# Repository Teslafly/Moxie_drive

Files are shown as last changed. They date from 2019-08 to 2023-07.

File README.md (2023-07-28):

# ABANDONED Moxie_drive
A motor drive based off https://github.com/vedderb/bldc-hardware capable of 75v and 100a continuous for silly electric vehicles

MoxiE-Drive - high power  motor controller
=============

design:
12-60v
120-150 continuous phase amps
based off the vesc 6. has phase shunts

Forged from the remminants of the oppressed vesc 6.
Raised on a diet of endless sphere and equals zero posts.
destined for a fight to the death in hilariously brutal Power Wheels Racing Series.
I give to you, the MoxiE-Drive.

This the Hardware for my derivitive of the Vesc-project.

## Schematic top level


## Layout -made with KiCad!-


## 3D views



Have a look at this post for a tutorial on how to get started:
http://vedder.se/2015/01/vesc-open-source-esc/

Made with KiCad 5

wonderfulfailure.wordpress.com

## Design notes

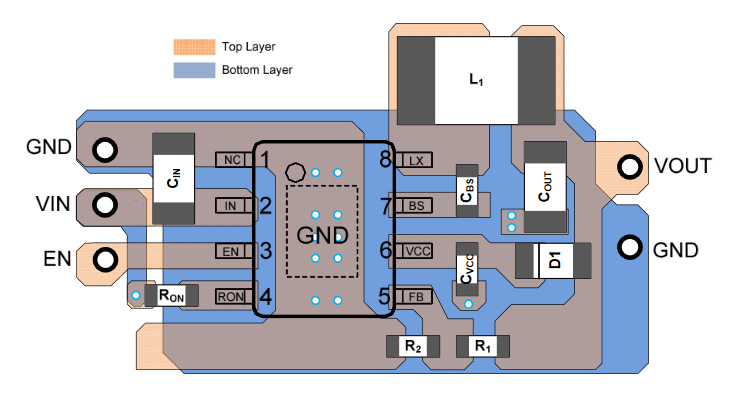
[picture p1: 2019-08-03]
Moxie_Power_stage/sy8502_hv_buck_layout.PNG

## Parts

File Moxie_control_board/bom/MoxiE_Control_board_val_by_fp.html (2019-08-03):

Ref | Qnty | Value | Part | Footprint | Description | Vendor
C101, C110, C304 | 3 | 100n | MoxiE_Control_board-rescue:C-Device | Capacitors_SMD:C_0402
C102, C106, C107, C108, C109, C111, C503, C506, C507 | 9 | 100nf | MoxiE_Control_board-rescue:C-Device | Capacitors_SMD:C_0402
C103, C104, C105, C203 | 4 | 4.7nf | MoxiE_Control_board-rescue:C-Device | Capacitors_SMD:C_0402
C201, C301, C302, C303, C305, C307, C309, C310, C311, C312 | 10 | 2.2u | MoxiE_Control_board-rescue:C-Device | Capacitors_SMD:C_0402
C306, C308 | 2 | 15p | MoxiE_Control_board-rescue:C-Device | Capacitors_SMD:C_0402
C501, C508 | 2 | 2.2uf | MoxiE_Control_board-rescue:C-Device | Capacitors_SMD:C_0603
C509 | 1 | 100uf | MoxiE_Control_board-rescue:CP-Device | Capacitors_Tantalum_SMD:CP_Tantalum_Case-B_EIA-3528-21_Reflow
C510 | 1 | NP | MoxiE_Control_board-rescue:C-Device | Capacitors_SMD:C_0402
D301 | 1 | TPD2EUSB30DRTR | MoxiE_drive-rescue:TPD2EUSB30DRTR-dk_TVS-Diodes | digikey-footprints:SOT-3
D302 | 1 | BLUE | MoxiE_Control_board-rescue:LED_ALT-Device | LEDs:LED_0603
D303 | 1 | GREEN | MoxiE_Control_board-rescue:LED_ALT-Device | LEDs:LED_0603
D304 | 1 | RED | MoxiE_Control_board-rescue:LED_ALT-Device | LEDs:LED_0603
F401 | 1 | 0.5A polyfuse | MoxiE_Control_board-rescue:Polyfuse_Small-Device | Resistors_SMD:R_1812
IC201 | 1 | TCAN332D | MoxiE_drive_symbol_lib:TCAN332D | SO8
J101 | 1 | USB_B_Micro | MoxiE_drive-rescue:USB_B_Micro-Connector_Specialized | Connectors_USB:USB_Micro-B_Vertical_Molex-105133-0001
J102 | 1 | Conn_02x14_Odd_Even | MoxiE_Control_board-rescue:Conn_02x14_Odd_Even-Connector_Generic | moxie-drive-custom:FLE-113-01-G-DV
J301 | 1 | SWD | MoxiE_Control_board-rescue:Conn_01x05-Connector_Generic | Connectors_JST:JST_SH_SM06B-SRSS-TB_06x1.00mm_Angled
J401, J402, J403 | 3 | Conn_01x02 | MoxiE_Control_board-rescue:Conn_01x02-Connector_Generic | Connectors_JST:JST_PH_B2B-PH-K_02x2.00mm_Straight
K101 | 1 | SERVO | MoxiE_Control_board-rescue:Conn_01x03-Connector_Generic | Connectors_JST:JST_PH_B3B-PH-K_03x2.00mm_Straight
L501 | 1 | 3.3uH | MoxiE_drive-rescue:INDUCTOR-MyCustomLib | Mas_custom_parts:L_Bourns_SRN-4018
P101 | 1 | CANBUS | MoxiE_Control_board-rescue:Conn_01x04-Connector_Generic | Connectors_JST:JST_PH_B4B-PH-K_04x2.00mm_Straight
P102 | 1 | Serial3 | MoxiE_Control_board-rescue:Conn_01x04-Connector_Generic | Connectors_JST:JST_SH_SM04B-SRSS-TB_04x1.00mm_Angled
P103 | 1 | CTRL_SIGNALS | MoxiE_Control_board-rescue:Conn_01x07-Connector_Generic | Connectors_JST:JST_PH_B7B-PH-K_07x2.00mm_Straight
P104 | 1 | SPI | MoxiE_Control_board-rescue:Conn_01x06-Connector_Generic | Connectors_JST:JST_SH_SM06B-SRSS-TB_06x1.00mm_Angled
P105 | 1 | Serial1/tim4 | MoxiE_Control_board-rescue:Conn_01x04-Connector_Generic | Connectors_JST:JST_SH_SM04B-SRSS-TB_04x1.00mm_Angled
P106 | 1 | I2C | MoxiE_Control_board-rescue:Conn_01x04-Connector_Generic | Connectors_JST:JST_SH_SM04B-SRSS-TB_04x1.00mm_Angled
P107 | 1 | HALL/Encoder | MoxiE_Control_board-rescue:Conn_01x06-Connector_Generic | Connectors_JST:JST_PH_B6B-PH-K_06x2.00mm_Straight
Q401, Q402 | 2 | IRLML6344TRPBF | MoxiE_drive-rescue:IRLML6344TRPBF-dk_Transistors-FETs-MOSFETs-Single | digikey-footprints:SOT-23-3
R101, R111, R112, R113, R114, R115, R116, R117, R118, R119 | 10 | 100R | MoxiE_Control_board-rescue:R-Device | Resistors_SMD:R_0402
R102, R103 | 2 | 100k | MoxiE_Control_board-rescue:R-Device | Resistors_SMD:R_0402
R104, R105 | 2 | 22R | MoxiE_Control_board-rescue:R-Device | Resistors_SMD:R_0402
R106, R107, R108 | 3 | 2k2 | MoxiE_Control_board-rescue:R-Device | Resistors_SMD:R_0402
R109 | 1 | 10k | MoxiE_Control_board-rescue:R-Device | Resistors_SMD:R_0402
R110 | 1 | 0R | MoxiE_Control_board-rescue:R-Device | Resistors_SMD:R_0402
R201, R202 | 2 | 120R | MoxiE_Control_board-rescue:R-Device | Resistors_SMD:R_0603
R301, R302, R303, R501 | 4 | 1k | MoxiE_Control_board-rescue:R-Device | Resistors_SMD:R_0402
R502 | 1 | R33.2k 0.1% | MoxiE_Control_board-rescue:R-Device | Resistors_SMD:R_0402
R503 | 1 | 10k 0.1% | MoxiE_Control_board-rescue:R-Device | Resistors_SMD:R_0402
U301 | 1 | STM32F40X_LQFP64 | MoxiE_drive_symbol_lib:STM32F40X_LQFP64 | crf1:lqfp64_pad_mod
U502 | 1 | TPS561201 | MoxiE_Control_board-rescue:TPS563200-Regulator_Switching | TO_SOT_Packages_SMD:SOT-23-6
X301 | 1 | 8MHz 10ppm | MoxiE_drive_symbol_lib:CRYSTAL_SMD | Oscillators:Oscillator_SMD_EuroQuartz_XO53-4pin_5.0x3.2mm

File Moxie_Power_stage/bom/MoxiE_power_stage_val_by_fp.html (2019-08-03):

Ref | Qnty | Value | Part | Footprint | Description | Vendor
C101, C102, C103, C104, C105 | 5 | 470uf 80v | Device:CP1 | Mas_custom_parts:CP_Radial_D12.5mm_P5.00mm | Polarised capacitor
C201 | 1 | 2.2uF_100V | Device:C | pkl_dipol:C_1206 | Unpolarized capacitor
C202 | 1 | 0.1uf_100V | Device:C | pkl_dipol:C_0603 | Unpolarized capacitor
C203 | 1 | 0.1uf | Device:C | pkl_dipol:R_0402 | Unpolarized capacitor
C204 | 1 | 0.1uf | Device:C | pkl_dipol:C_0402 | Unpolarized capacitor
C205 | 1 | 4.7nf | Device:C | pkl_dipol:C_0402 | Unpolarized capacitor
C206, C301, C310, C401, C410, C501, C510 | 7 | 1uf | Device:C | pkl_dipol:C_0603 | Unpolarized capacitor
C207 | 1 | 100uf 25v | Device:CP1 | Capacitors_THT:CP_Radial_D8.0mm_P3.50mm | Polarised capacitor
C302, C303, C304, C305, C306, C307, C308, C309, C311, C402, C403, C404, C405, C406, C407, C408, C409, C411, C502, C503, C504, C505, C506, C507, C508, C509, C511 | 27 | 100v_1.0uF | Device:C | pkl_dipol:C_1206 | Unpolarized capacitor
C315, C415, C515 | 3 | 2.2u | Device:C | pkl_dipol:C_0402 | Unpolarized capacitor
D201 | 1 | 100v 200ma | Device:D | Diodes_SMD:D_SOD-323 | Diode
J101 | 1 | Conn_02x13_Counter_Clockwise | Connector_Generic:Conn_02x13_Counter_Clockwise | moxie-drive-custom:FLE-113-01-G-DV | Generic connector, double row, 02x13, counter clockwise pin numbering scheme (similar to DIP packge numbering), script generated (kicad-library-utils/schlib/autogen/connector/)
J201, J202 | 2 | Conn_01x02 | Connector_Generic:Conn_01x02 | Connectors_JST:JST_PH_B2B-PH-K_02x2.00mm_Straight | Generic connector, single row, 01x02, script generated (kicad-library-utils/schlib/autogen/connector/)
L201 | 1 | 100uh 2.5A | Device:L_Core_Ferrite | Inductors_SMD:L_12x12mm_h8mm | Inductor with Ferrite Core
MK101, MK102 | 2 | Mounting_Hole | Mechanical:Mounting_Hole | Mounting_Holes:MountingHole_3.2mm_M3 | Mounting Hole without connection
MK103, MK104, MK105, MK106 | 4 | Mounting_Hole | Mechanical:Mounting_Hole | Mounting_Holes:MountingHole_3.2mm_M3_Pad_Via | Mounting Hole without connection
NT301, NT401, NT501 | 3 | Net-Tie_2 | Device:Net-Tie_2 | NetTie:NetTie-2_SMD_Pad0.5mm | Net Tie, 2 pins
P101, P102, P105 | 3 | PHASE_3 | Connector_Generic:Conn_01x01 | Mas_custom_parts:large_wire_pad | Generic connector, single row, 01x01, script generated (kicad-library-utils/schlib/autogen/connector/)
P103 | 1 | PHASE_1 | Connector_Generic:Conn_01x01 | Mas_custom_parts:large_wire_pad | Generic connector, single row, 01x01, script generated (kicad-library-utils/schlib/autogen/connector/)
P104 | 1 | PHASE_2 | Connector_Generic:Conn_01x01 | Mas_custom_parts:large_wire_pad | Generic connector, single row, 01x01, script generated (kicad-library-utils/schlib/autogen/connector/)
Q301, Q302, Q303, Q304, Q305, Q306, Q401, Q402, Q403, Q404, Q405, Q406, Q501, Q502, Q503, Q504, Q505, Q506 | 18 | TPH2R608NH,L1Q | Device:Q_NMOS_DGS | moxie-drive-custom:SOP8_Advance | Transistor N-MOSFET (general)
R101 | 1 | 100k | Device:R | pkl_dipol:R_0402 | Resistor
R102 | 1 | 1k | Device:R | pkl_dipol:R_0402 | Resistor
R201 | 1 | 100k | Device:R | pkl_dipol:R_0603 | Resistor
R202, R601 | 2 | 10k | Device:R | pkl_dipol:R_0402 | Resistor
R203 | 1 | 2MΩ | Device:R | pkl_dipol:R_0603 | Resistor
R204 | 1 | 20k | Device:R | pkl_dipol:R_0402 | Resistor
R205 | 1 | 2.2k | Device:R | pkl_dipol:R_0402 | Resistor
R301, R302, R401, R402, R501, R502 | 6 | 2k2 | Device:R | pkl_dipol:R_0402 | Resistor
R303, R304, R305, R306, R307, R308, R403, R404, R405, R406, R407, R408, R503, R504, R505, R506, R507, R508 | 18 | 10R | Device:R | pkl_dipol:R_0402 | Resistor
R309, R312, R409, R412, R509, R512 | 6 | 1.0mΩ | Device:R | NetTie:NetTie-2_SMD_Pad2.0mm | Resistor
R310, R410, R510 | 3 | 0.5mΩ | Device:R | moxie-drive-custom:R_2512_shunt_vishay | Resistor
R311, R411, R511 | 3 | 1.0mΩ | Device:R | moxie-drive-custom:R_2512_shunt_vishay | Resistor
R313, R413, R513, R603, R605 | 5 | 39k | Device:R | pkl_dipol:R_0603 | Resistor
R314, R414, R514, R604, R606 | 5 | 2k2 | Device:R | pkl_dipol:R_0603 | Resistor
R602 | 1 | 10k ntc | Device:R | pkl_dipol:R_0402 | Resistor
U201 | 1 | SY8502 | MoxiE_power_stage-rescue:SY8502-MAS_Power | Mas_custom_parts:SO8-E
U301, U401, U501 | 3 | MIC4605-1YMT | MoxiE_power_stage-rescue:MIC4065-1YMT-MAS_Power | moxie-drive-custom:TDFN2525-10ld
U302, U402, U502 | 3 | ACS711 | MoxiE_power_stage-rescue:ACS711-MAS_Power | Mas_custom_parts:ACS711KEX

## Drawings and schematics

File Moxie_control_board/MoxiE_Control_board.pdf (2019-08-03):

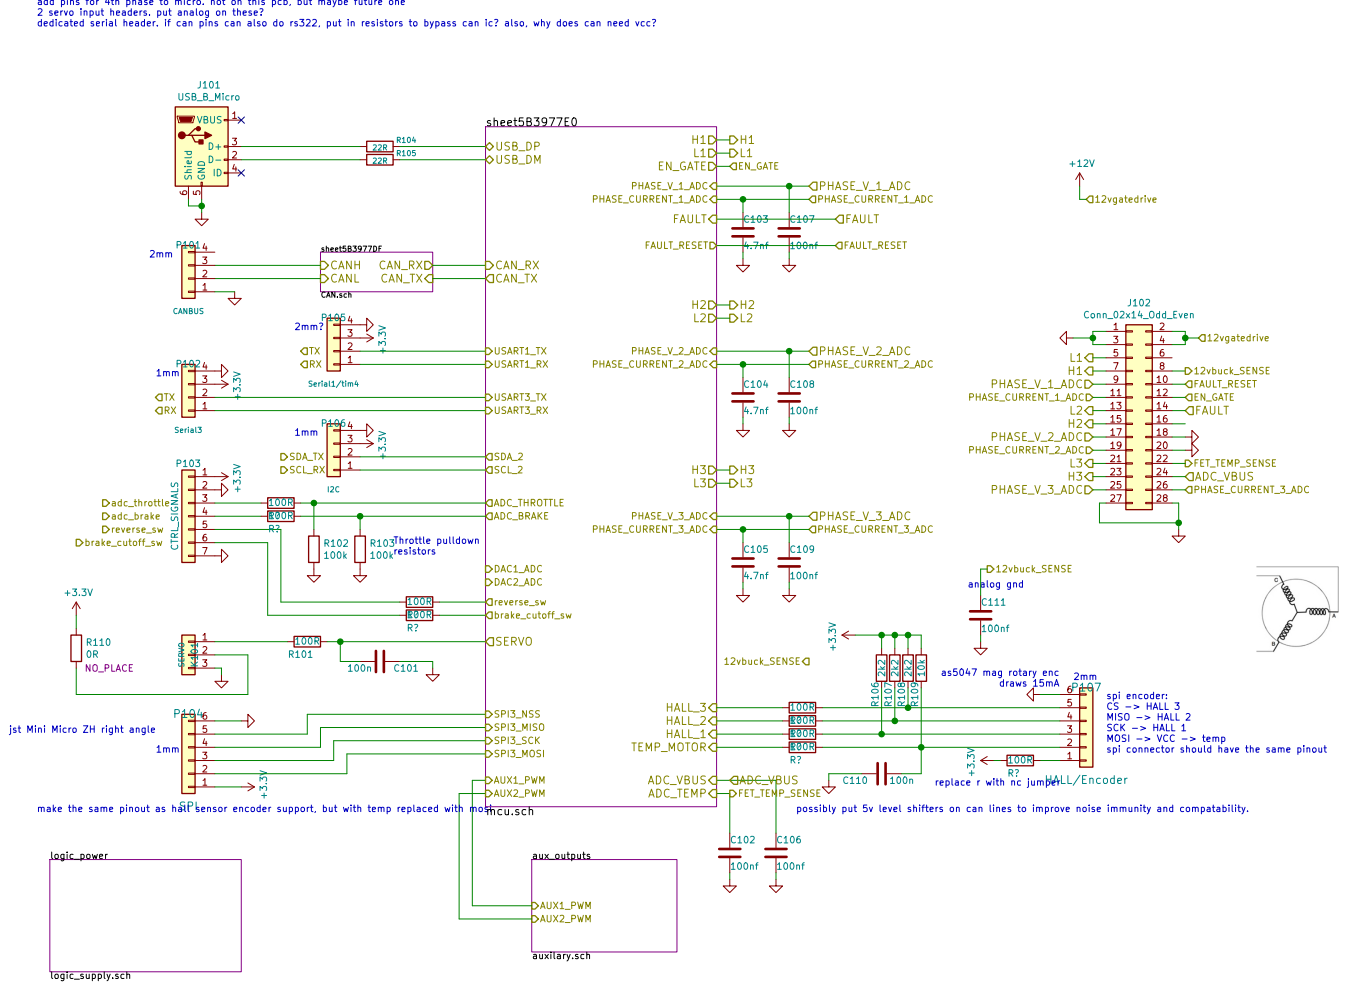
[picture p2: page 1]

add pins for 4th phase to micro. not on this pcb, but maybe future one
2 servo input headers. put analog on these?
dedicated serial header. if can pins can also do rs322, put in resistors to bypass can ic? also, why does can need vcc?

as5047 mag rotary enc draws 15mA

spi encoder: CS -> HALL 3 MISO -> HALL 2 SCK -> HALL 1 MOSI -> VCC -> temp

jst Mini Micro ZH right angle

replace r with nc jumper

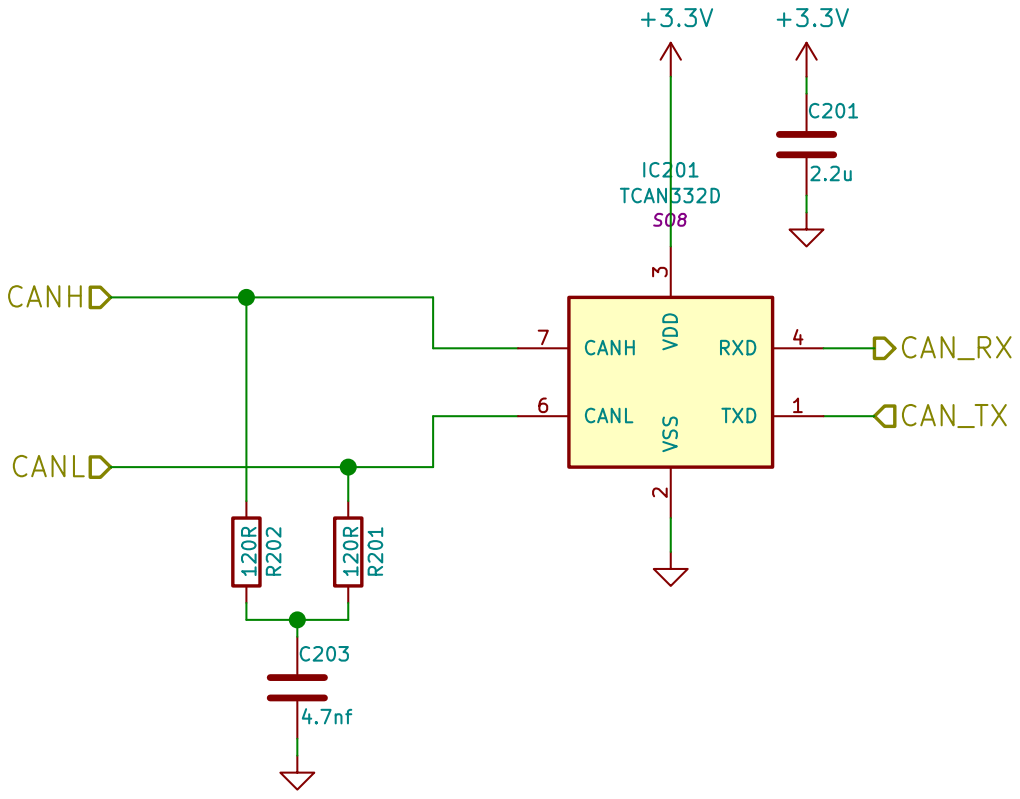
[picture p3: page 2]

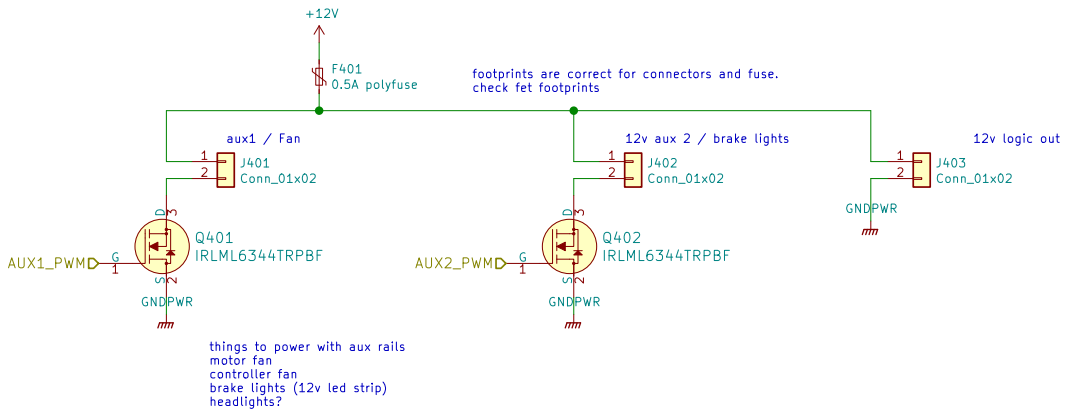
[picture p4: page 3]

footprints are correct for connectors and fuse.
check fet footprints

things to power with aux rails motor fan

controller fan
brake lights (12v led strip)

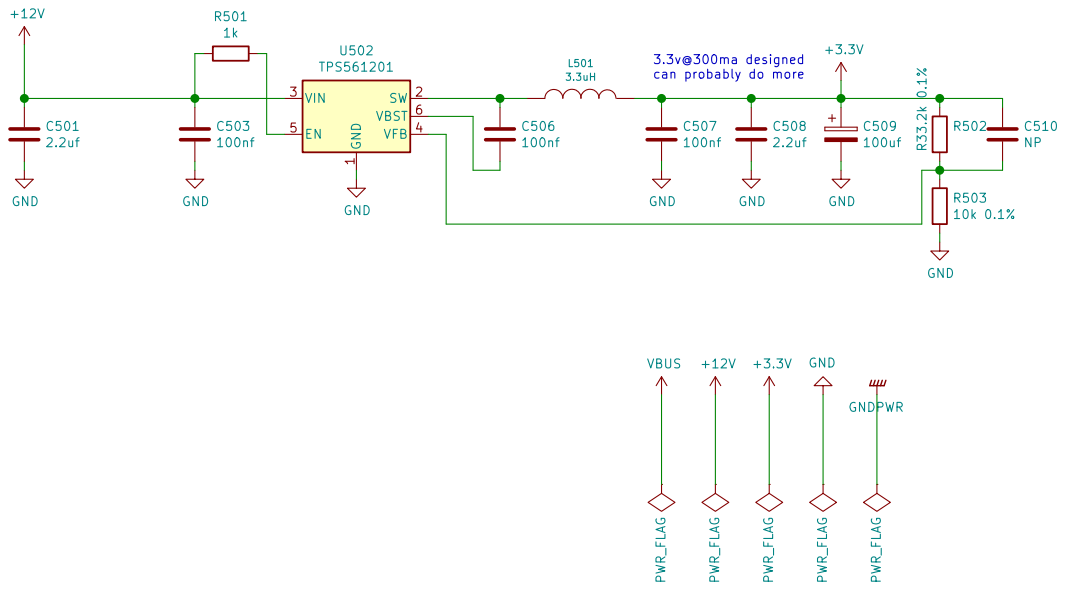
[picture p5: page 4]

can probably do more C501

1 SW 2 VIN 3 VFB 4 EN 5 VBST 6 U502 TPS561201 L501

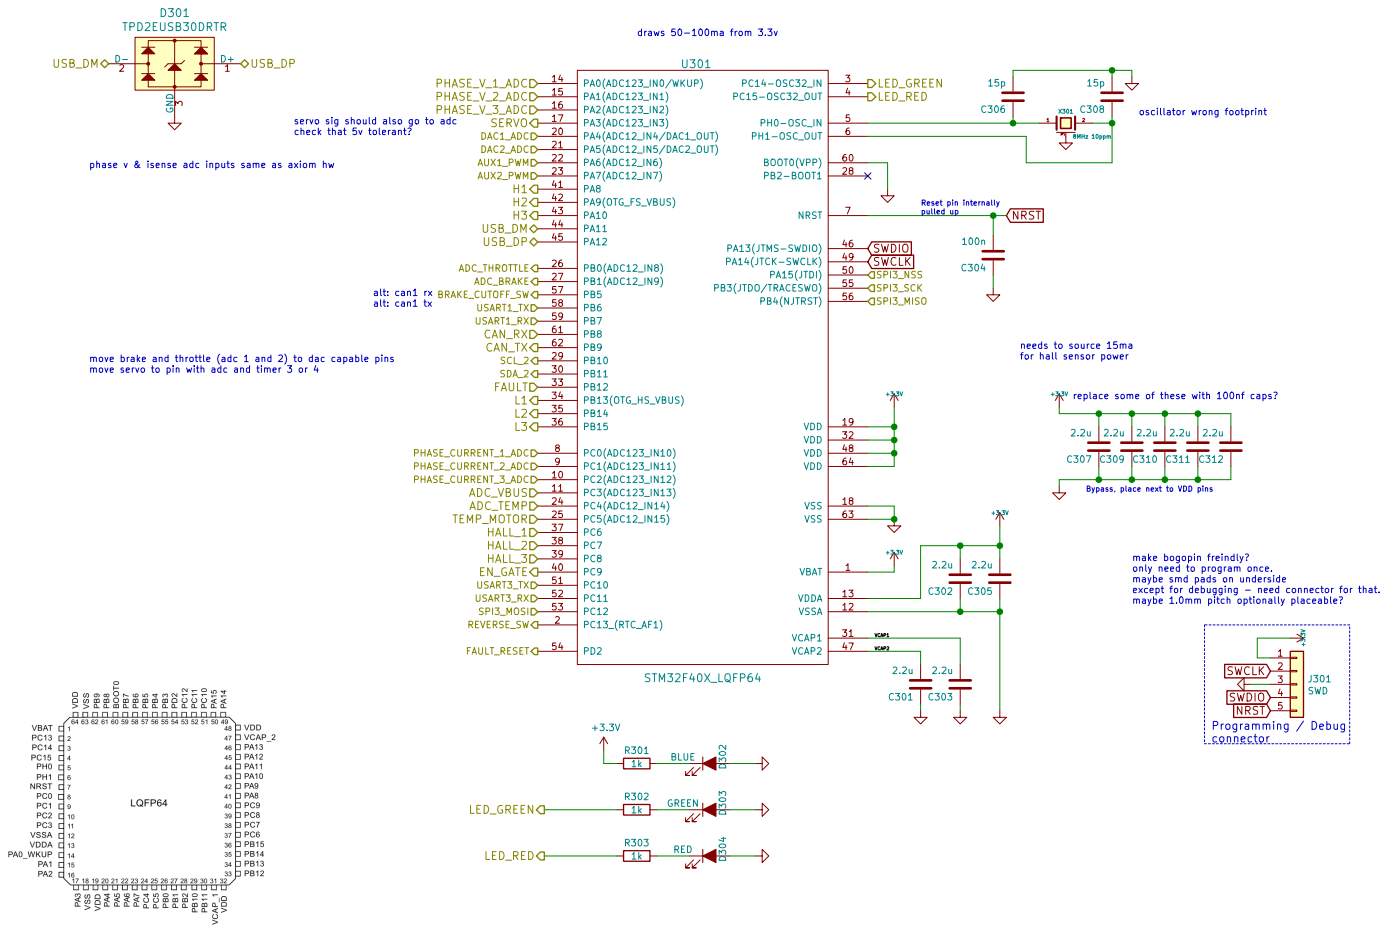
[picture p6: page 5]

replace some of these with 100nf caps? SPI3_NSS

servo sig should also go to adc

phase v & isense adc inputs same as axiom hw

alt: can1 rx alt: can1 tx

Bypass, place next to VDD pins CAN_RX
CAN_TX

move brake and throttle (adc 1 and 2) to dac capable pins
move servo to pin with adc and timer 3 or 4

only need to program once.
maybe smd pads on underside
except for debugging - need connector for that.

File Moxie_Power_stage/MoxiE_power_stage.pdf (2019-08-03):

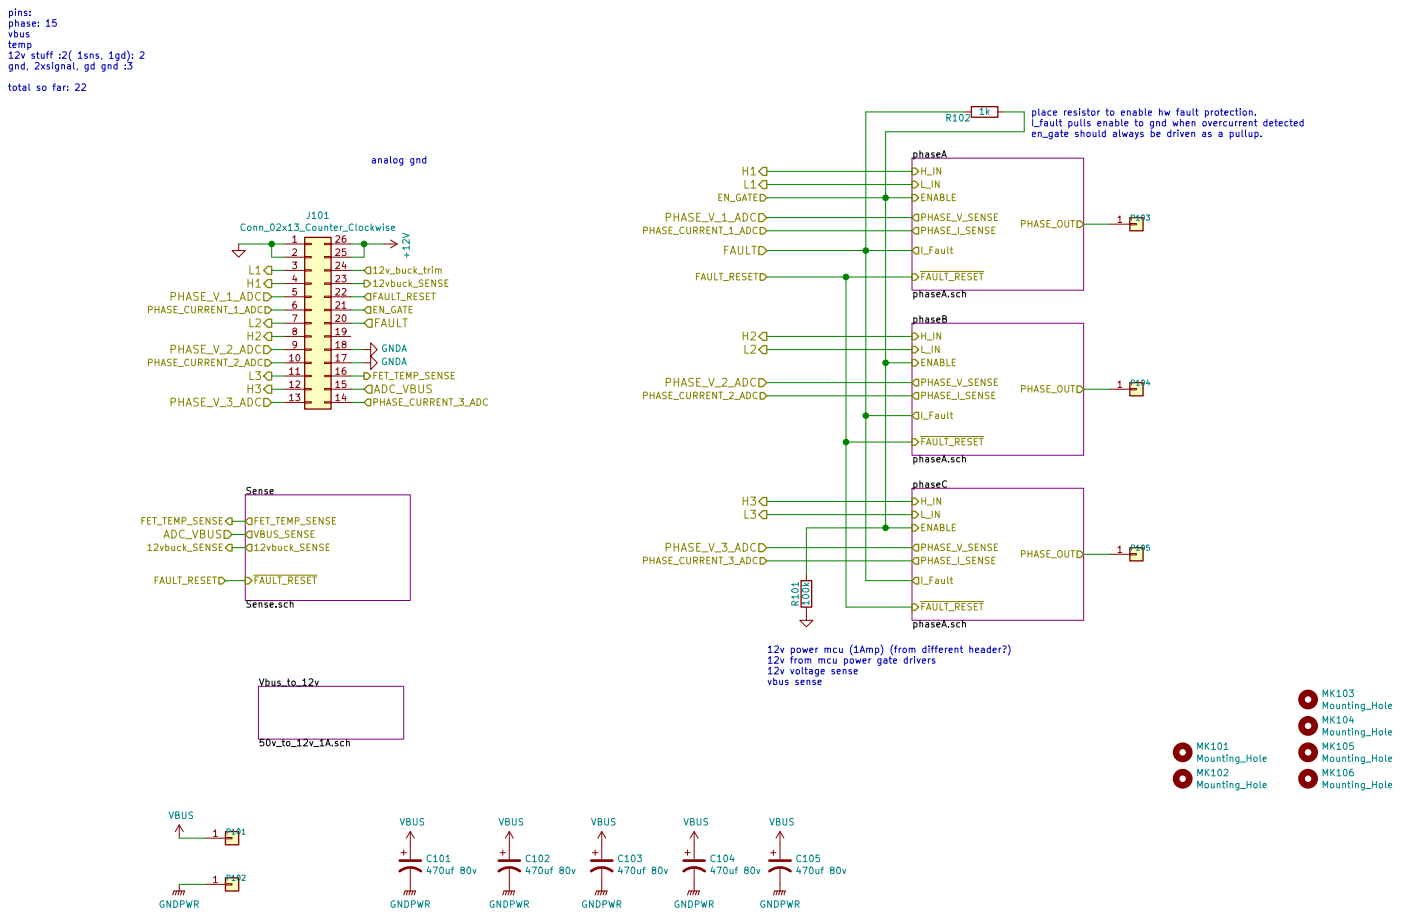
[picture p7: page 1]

I_fault pulls enable to gnd when overcurrent detected
en_gate should always be driven as a pullup.

12v from mcu power gate drivers
12v voltage sense

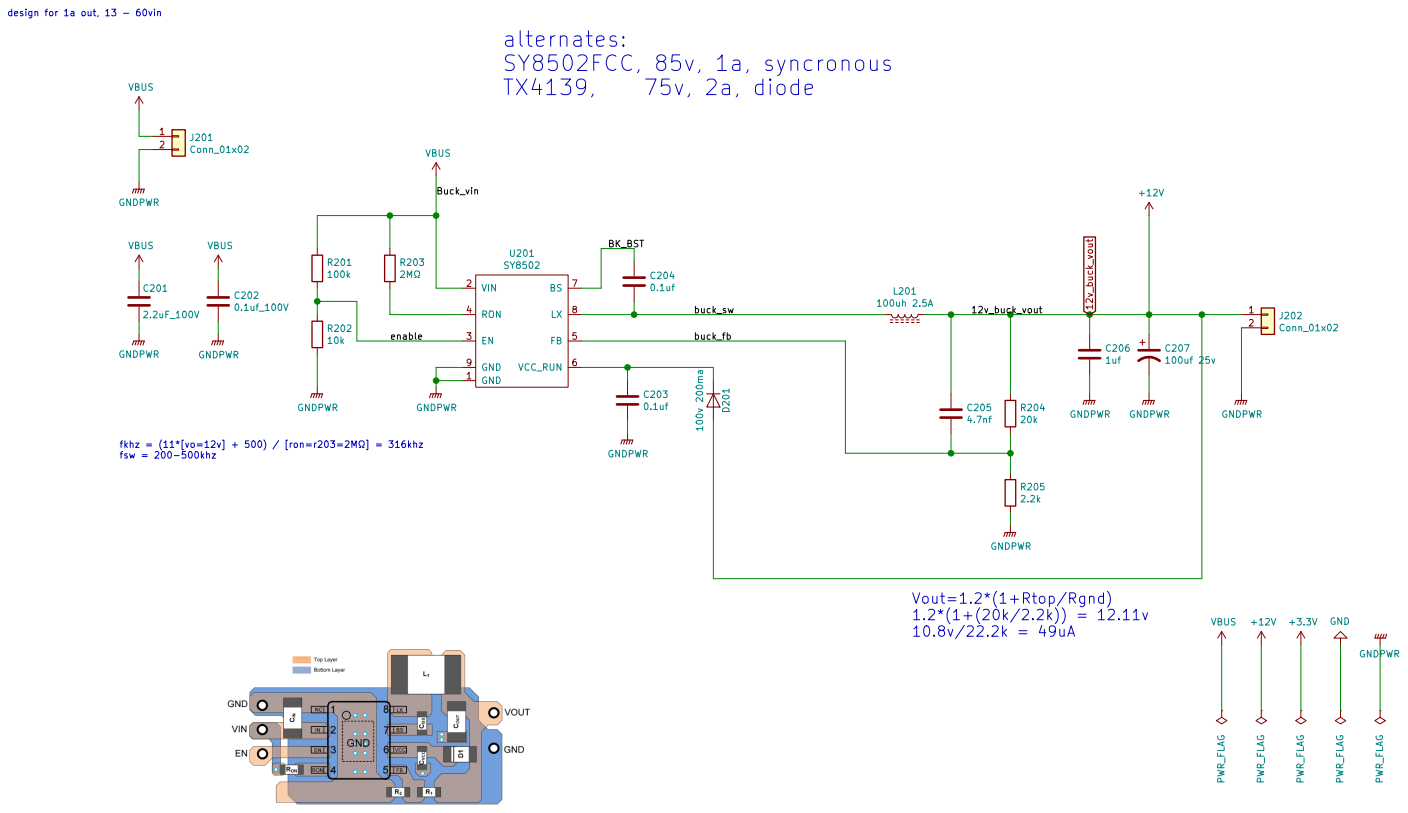
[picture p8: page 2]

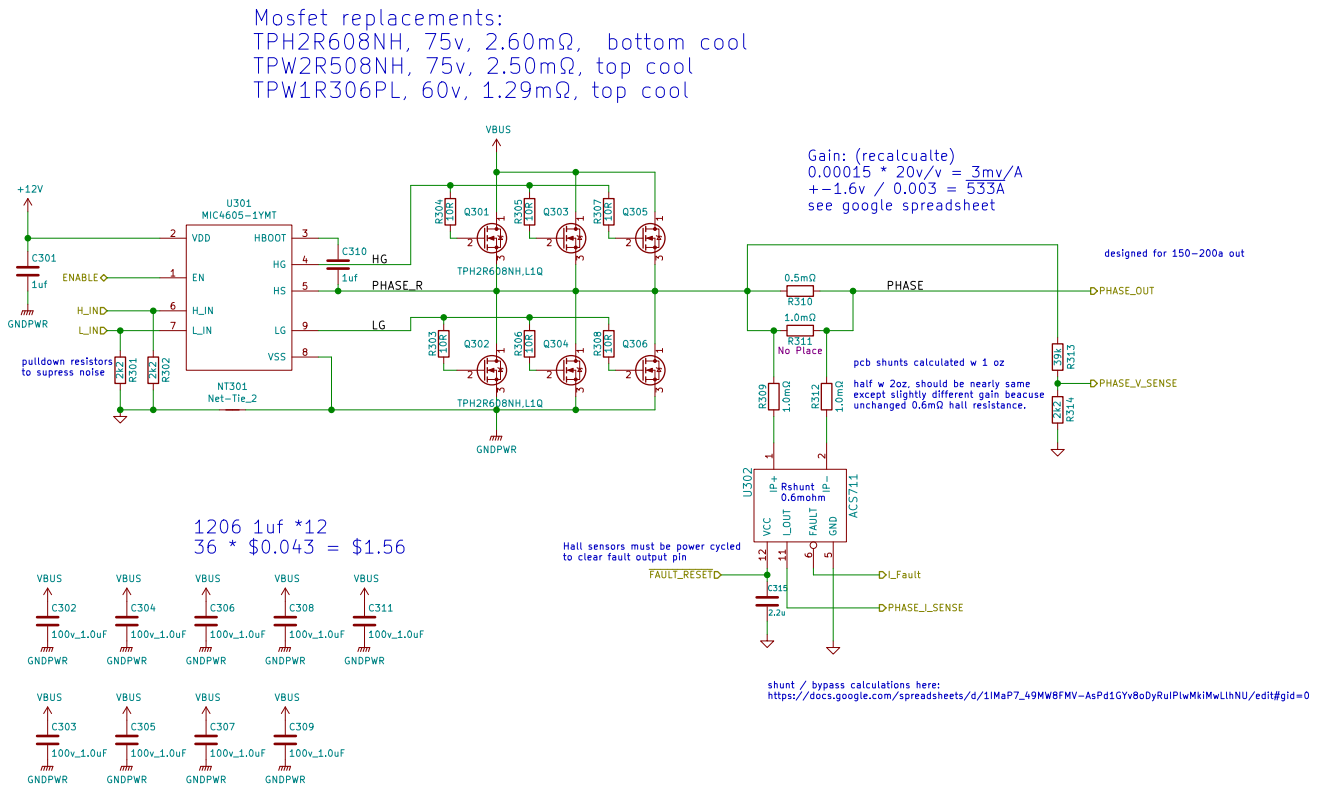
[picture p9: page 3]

pcb shunts calculated w 1 oz

half w 2oz, should be nearly same
except slightly different gain beacuse

FAULT_RESET Hall sensors must be power cycled

shunt / bypass calculations here:
https://docs.google.com/spreadsheets/d/1IMaP7_49MW8FMV-AsPd1GYv8oDyRuIPlwMkiMwLlhNU/edit#gid=0

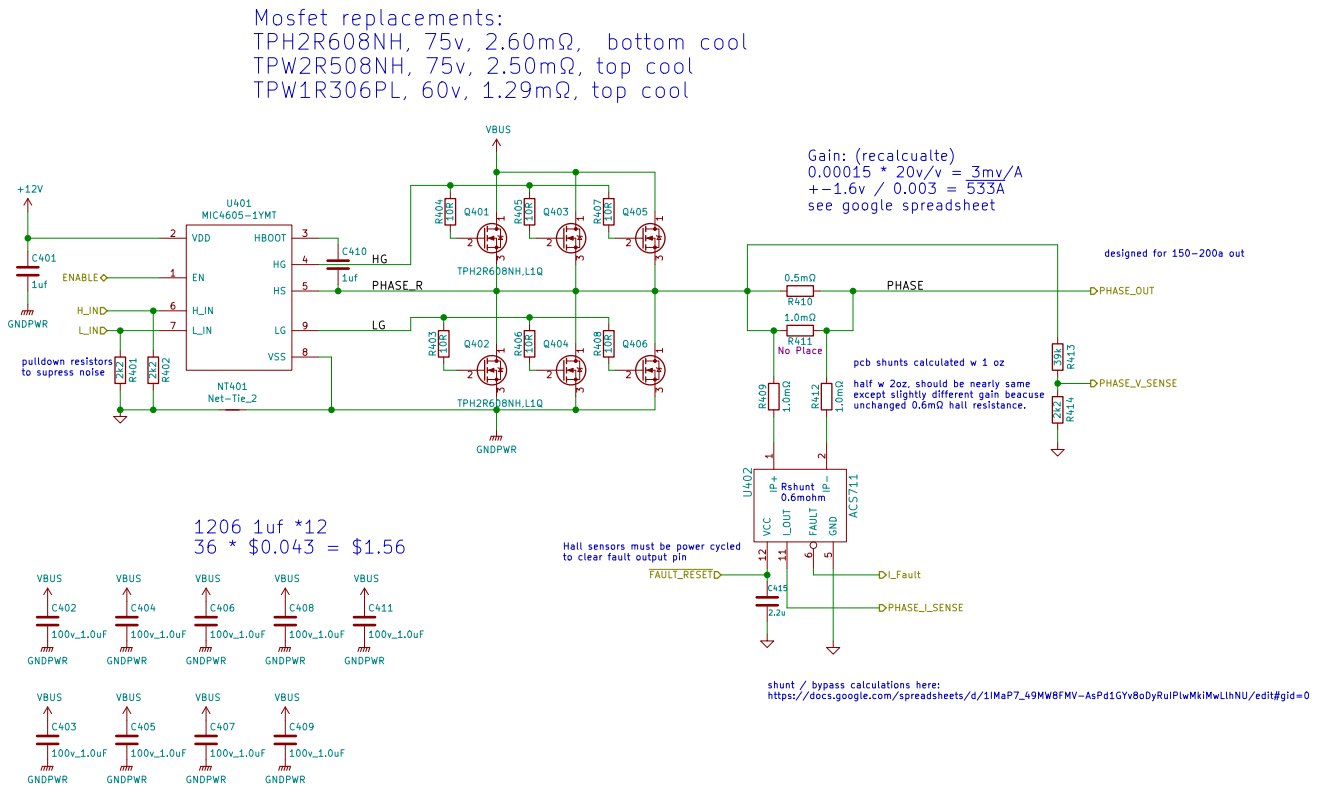
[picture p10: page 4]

pcb shunts calculated w 1 oz

half w 2oz, should be nearly same
except slightly different gain beacuse

FAULT_RESET Hall sensors must be power cycled

shunt / bypass calculations here:
https://docs.google.com/spreadsheets/d/1IMaP7_49MW8FMV-AsPd1GYv8oDyRuIPlwMkiMwLlhNU/edit#gid=0

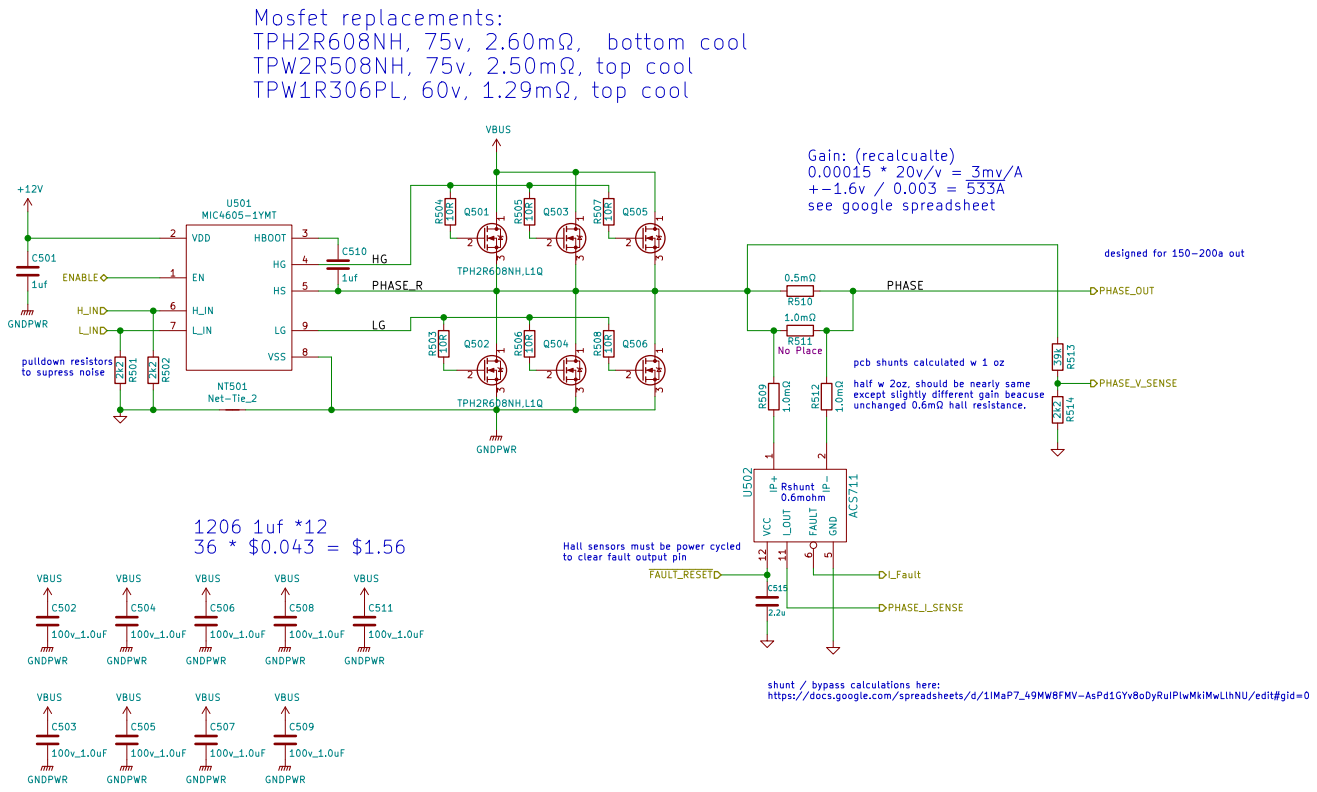
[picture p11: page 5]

pcb shunts calculated w 1 oz

half w 2oz, should be nearly same
except slightly different gain beacuse

FAULT_RESET Hall sensors must be power cycled

shunt / bypass calculations here:
https://docs.google.com/spreadsheets/d/1IMaP7_49MW8FMV-AsPd1GYv8oDyRuIPlwMkiMwLlhNU/edit#gid=0

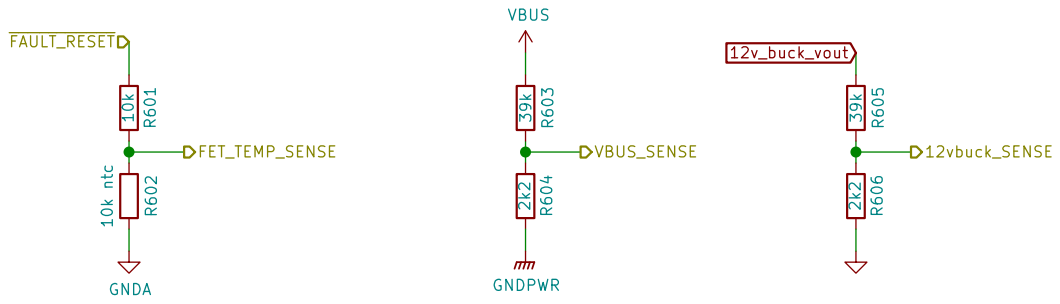
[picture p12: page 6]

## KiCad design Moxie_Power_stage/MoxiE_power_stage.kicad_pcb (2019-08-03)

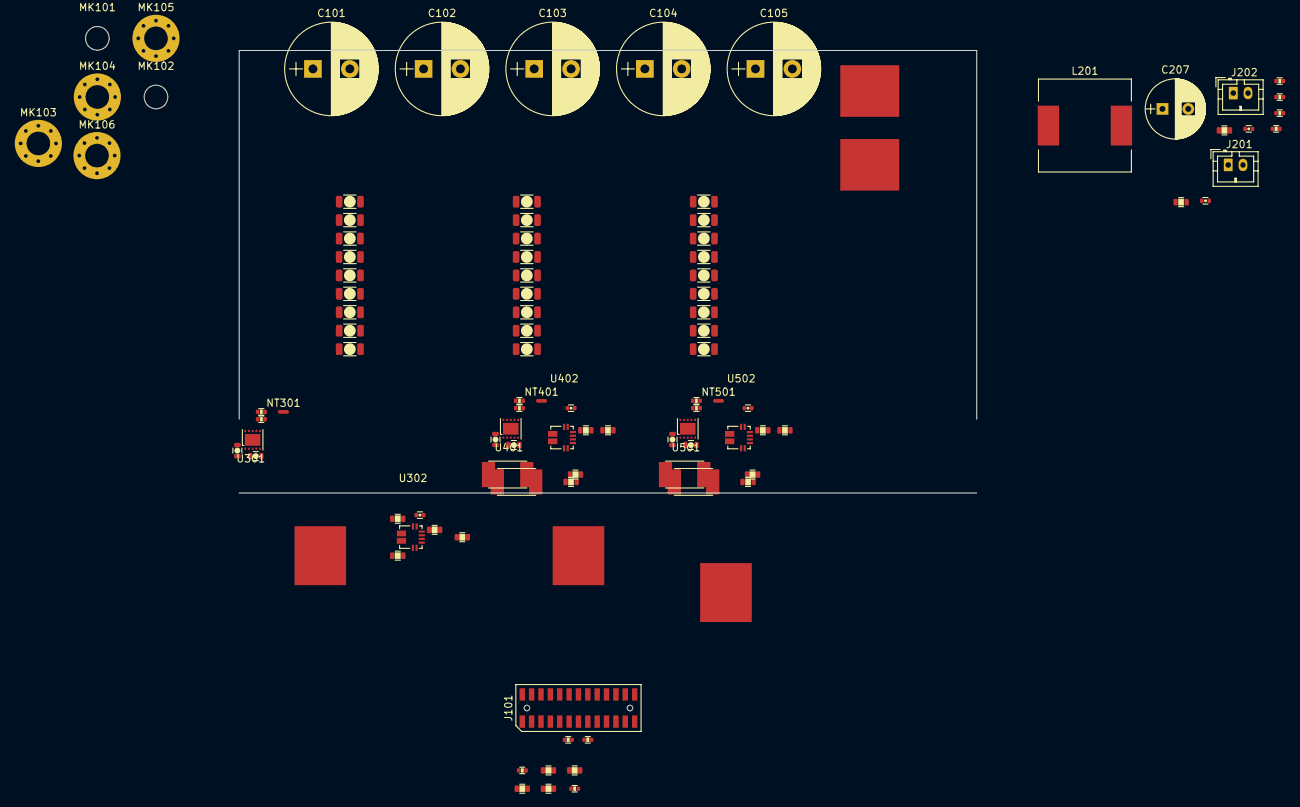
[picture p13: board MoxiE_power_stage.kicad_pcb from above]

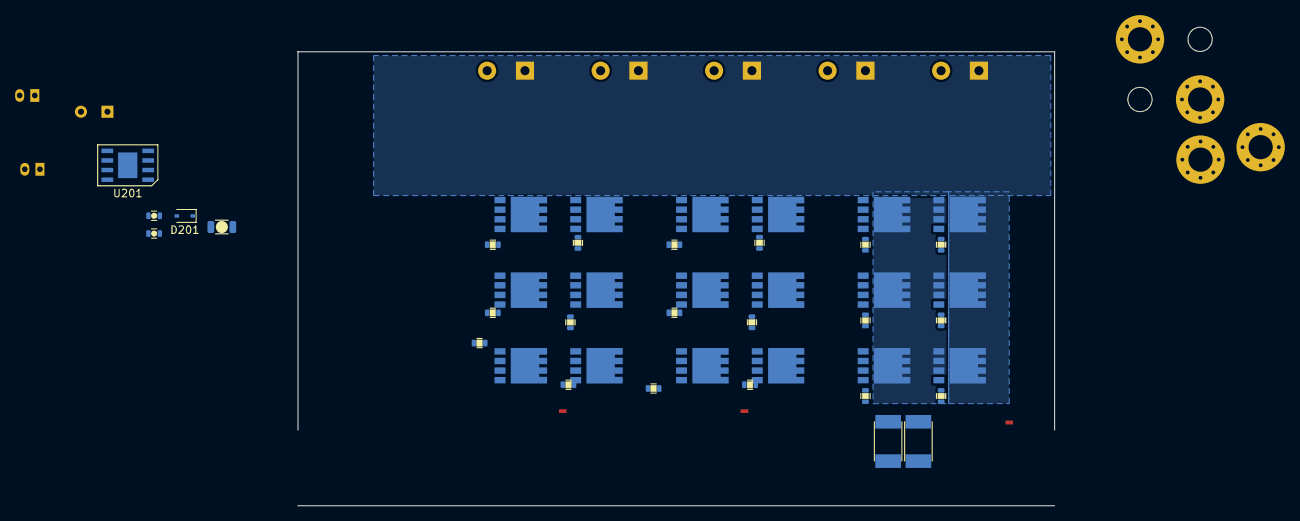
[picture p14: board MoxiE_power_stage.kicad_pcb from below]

Board: 4 copper layers, 100.0 x 60.0 mm, 147 parts (43 on the bottom side), 68 nets, no tracks yet.

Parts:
C101, C102, C103, C104, C105: 470uf 80v; CP_Radial_D12.5mm_P5.00mm
C201: 2.2uF_100V; C_1206
C202: 0.1uf_100V; C_0603
C203: 0.1uf; R_0402
C204: 0.1uf; C_0402
C205: 4.7nf; C_0402
C206, C301, C310, C401, C410, C501, C510: 1uf; C_0603
C207: 100uf 25v; CP_Radial_D8.0mm_P3.50mm
C302, C303, C304, C305, C306, C307, C308, C309, C311, C402, C403, C404, C405, C406, C407, C408, C409, C411, C502, C503, C504, C505, C506, C507, C508, C509, C511: 100v_1.0uF; C_1206
C315, C415, C515: 2.2u; C_0402
D201: 100v 200ma; D_SOD-323
J101: Conn_02x13_Counter_Clockwise; FLE-113-01-G-DV
J201, J202: Conn_01x02; JST_PH_B2B-PH-K_02x2.00mm_Straight
L201: 100uh 2.5A; L_12x12mm_h8mm
MK101, MK102: Mounting_Hole; MountingHole_3.2mm_M3
MK103, MK104, MK105, MK106: Mounting_Hole; MountingHole_3.2mm_M3_Pad_Via
NT301, NT401, NT501: Net-Tie_2; NetTie-2_SMD_Pad0.5mm
P101, P102, P105: PHASE_3; large_wire_pad
P103: PHASE_1; large_wire_pad
P104: PHASE_2; large_wire_pad
Q301, Q302, Q303, Q304, Q305, Q306, Q401, Q402, Q403, Q404, Q405, Q406, Q501, Q502, Q503, Q504, Q505, Q506: TPH2R608NH,L1Q; SOP8_Advance
R101: 100k; R_0402
R102: 1k; R_0402
R201: 100k; R_0603
R202, R601: 10k; R_0402
R203: 2MΩ; R_0603
R204: 20k; R_0402
R205: 2.2k; R_0402
R301, R302, R401, R402, R501, R502: 2k2; R_0402
R303, R304, R305, R306, R307, R308, R403, R404, R405, R406, R407, R408, R503, R504, R505, R506, R507, R508: 10R; R_0603
R309, R312, R409, R412, R509, R512: 1.0mΩ; R_0603
R310, R410, R510: 0.5mΩ; R_2512_shunt_vishay
R311, R411, R511: 1.0mΩ; R_2512_shunt_vishay
R313, R413, R513, R603, R605: 39k; R_0603
R314, R414, R514, R604, R606: 2k2; R_0603
R602: 10k ntc; R_0402
U201: SY8502; SO8-E
U301, U401, U501: MIC4605-1YMT; TDFN2525-10ld
U302, U402, U502: ACS711; ACS711KEX

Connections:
12v_buck_vout: C205.1, C206.1, C207.1, C301.1, C401.1, C501.1, D201.2, J101.25, J101.26, J202.1, L201.1, R204.1, R605.2, U301.2, U401.2, U501.2
/12vbuck_SENSE: J101.23, R605.1, R606.1
/ADC_VBUS: J101.15, R603.1, R604.1
/EN_GATE: J101.21, R101.2, R102.2, U301.1, U401.1, U501.1
/FAULT: J101.20, R102.1, U302.6, U402.6, U502.6
/FAULT_RESET: C315.1, C415.1, C515.1, J101.22, R601.1, U302.12, U402.12, U502.12
/FET_TEMP_SENSE: J101.16, R601.2, R602.2
/H1: J101.4, R302.1, U301.6
/H2: J101.8, R402.1, U401.6
/H3: J101.12, R502.1, U501.6
/L1: J101.3, R301.1, U301.7
/L2: J101.7, R401.1, U401.7
/L3: J101.11, R501.1, U501.7
/PHASE_CURRENT_1_ADC: J101.6, U302.11
/PHASE_CURRENT_2_ADC: J101.10, U402.11
/PHASE_CURRENT_3_ADC: J101.14, U502.11
/PHASE_V_1_ADC: J101.5, R313.1, R314.1
/PHASE_V_2_ADC: J101.9, R413.1, R414.1
/PHASE_V_3_ADC: J101.13, R513.1, R514.1
/Vbus_to_12v/BK_BST: C204.1, U201.7
/Vbus_to_12v/buck_fb: C205.2, R204.2, R205.1, U201.5
/Vbus_to_12v/buck_sw: C204.2, L201.2, U201.8
/Vbus_to_12v/enable: R201.2, R202.1, U201.3
/phaseA/HG: R304.2, R305.2, R307.2, U301.4
/phaseA/LG: R303.2, R306.2, R308.2, U301.9
/phaseA/PHASE_OUT: P103.1, R310.1, R311.1, R312.2
/phaseA/PHASE_R: C310.2, Q301.3, Q302.1, Q303.3, Q304.1, Q305.3, Q306.1, R309.2, R310.2, R311.2, R313.2, U301.5
/phaseB/HG: R404.2, R405.2, R407.2, U401.4
/phaseB/LG: R403.2, R406.2, R408.2, U401.9
/phaseB/PHASE_OUT: P104.1, R410.1, R411.1, R412.2
/phaseB/PHASE_R: C410.2, Q401.3, Q402.1, Q403.3, Q404.1, Q405.3, Q406.1, R409.2, R410.2, R411.2, R413.2, U401.5
/phaseC/HG: R504.2, R505.2, R507.2, U501.4
/phaseC/LG: R503.2, R506.2, R508.2, U501.9
/phaseC/PHASE_OUT: P105.1, R510.1, R511.1, R512.2
/phaseC/PHASE_R: C510.2, Q501.3, Q502.1, Q503.3, Q504.1, Q505.3, Q506.1, R509.2, R510.2, R511.2, R513.2, U501.5
GND: C315.2, C415.2, C515.2, J101.1, J101.2, NT301.1, NT401.1, NT501.1, R101.1, R301.2, R302.2, R314.2, R401.2, R402.2, R414.2, R501.2, R502.2, R514.2, R606.2, U302.5, U402.5, U502.5
GNDA: J101.17, J101.18, R602.1
GNDPWR: C101.2, C102.2, C103.2, C104.2, C105.2, C201.2, C202.2, C203.2, C206.2, C207.2, C301.2, C302.2, C303.2, C304.2, C305.2, C306.2, C307.2, C308.2, C309.2, C311.2, C401.2, C402.2, C403.2, C404.2, C405.2, C406.2, C407.2, C408.2, C409.2, C411.2, C501.2, C502.2, C503.2, C504.2, C505.2, C506.2, C507.2, C508.2, C509.2, C511.2, J201.2, J202.2, NT301.2, NT401.2, NT501.2, P102.1, Q302.3, Q304.3, Q306.3, Q402.3, Q404.3, Q406.3, Q502.3, Q504.3, Q506.3, R202.2, R205.2, R604.2, U201.1, U201.9, U301.8, U301.11, U401.8, U401.11, U501.8, U501.11
unnamed: C203.1, D201.1, U201.6
unnamed: C310.1, U301.3
unnamed: C410.1, U401.3
unnamed: C510.1, U501.3
unnamed: Q301.2, R304.1
unnamed: Q302.2, R303.1
unnamed: Q303.2, R305.1
unnamed: Q304.2, R306.1
unnamed: Q305.2, R307.1
unnamed: Q306.2, R308.1
unnamed: Q401.2, R404.1
unnamed: Q402.2, R403.1
unnamed: Q403.2, R405.1
unnamed: Q404.2, R406.1
unnamed: Q405.2, R407.1
unnamed: Q406.2, R408.1
unnamed: Q501.2, R504.1
unnamed: Q502.2, R503.1
unnamed: Q503.2, R505.1
unnamed: Q504.2, R506.1
unnamed: Q505.2, R507.1
unnamed: Q506.2, R508.1
unnamed: R203.2, U201.4
unnamed: R309.1, U302.1
unnamed: R312.1, U302.2
unnamed: R409.1, U402.1
unnamed: R412.1, U402.2
unnamed: R509.1, U502.1
unnamed: R512.1, U502.2
VBUS: C101.1, C102.1, C103.1, C104.1, C105.1, C201.1, C202.1, C302.1, C303.1, C304.1, C305.1, C306.1, C307.1, C308.1, C309.1, C311.1, C402.1, C403.1, C404.1, C405.1, C406.1, C407.1, C408.1, C409.1, C411.1, C502.1, C503.1, C504.1, C505.1, C506.1, C507.1, C508.1, C509.1, C511.1, J201.1, P101.1, Q301.1, Q303.1, Q305.1, Q401.1, Q403.1, Q405.1, Q501.1, Q503.1, Q505.1, R201.1, R203.1, R603.2, U201.2

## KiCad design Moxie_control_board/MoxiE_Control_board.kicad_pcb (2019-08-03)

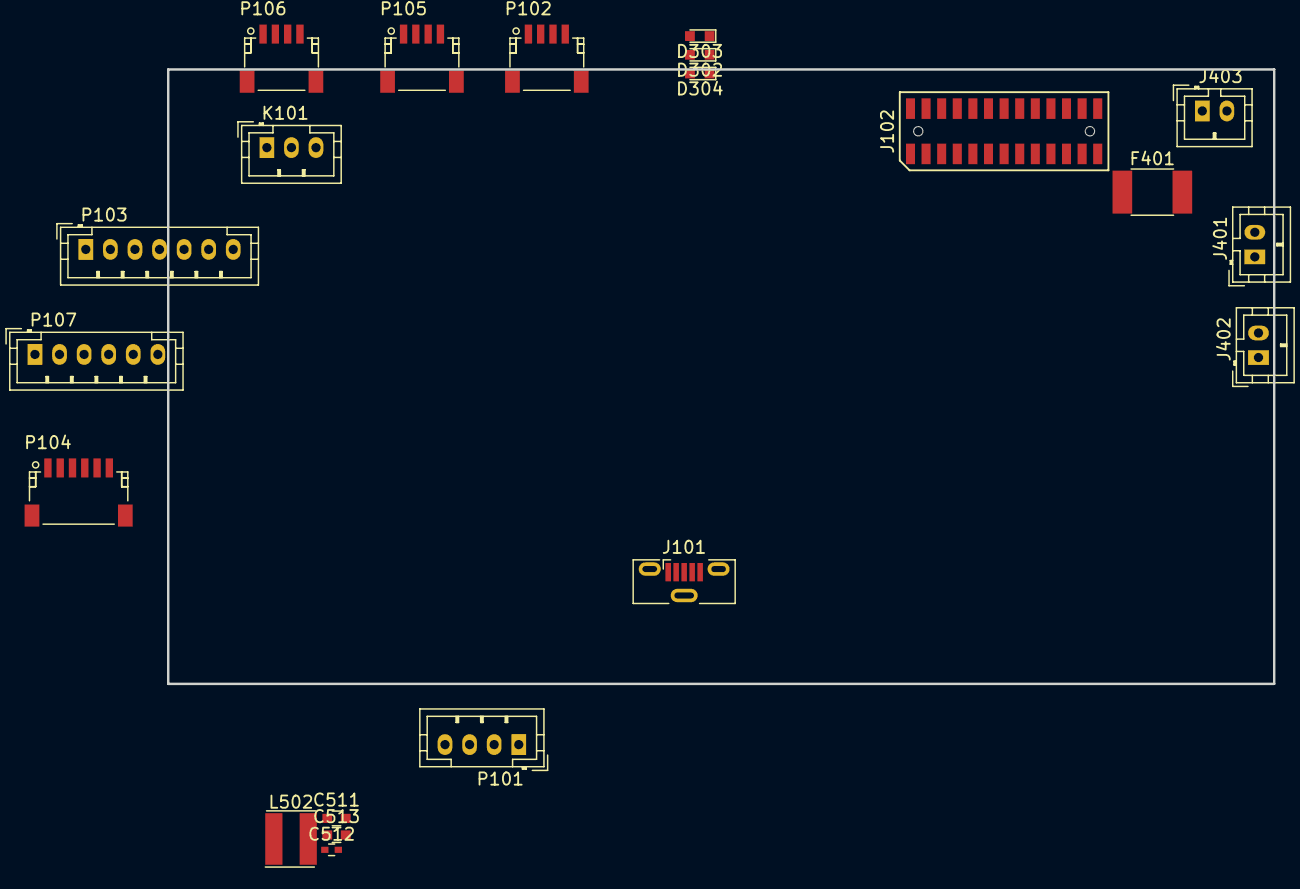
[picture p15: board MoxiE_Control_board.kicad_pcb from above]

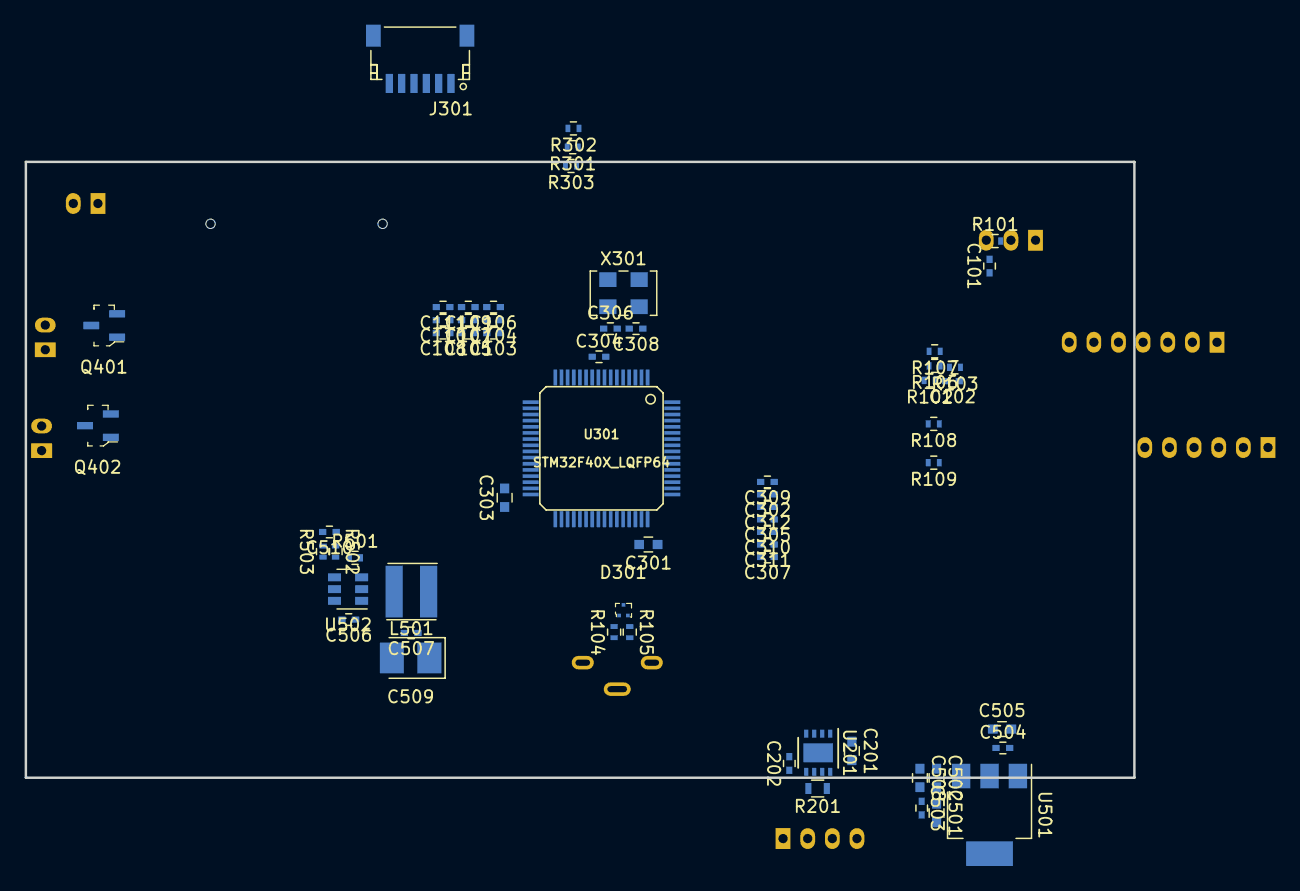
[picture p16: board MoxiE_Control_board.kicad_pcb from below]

Board: 2 copper layers, 90.0 x 50.0 mm, 82 parts (61 on the bottom side), 62 nets, no tracks yet.

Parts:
C101, C110, C304: 100n; C_0402
C102, C106, C107, C108, C109, C111, C202, C503, C506, C507: 100nf; C_0402
C103, C104, C105: 4.7nf; C_0402
C201, C301, C303, C502, C511: 2.2u; C_0603
C302, C305, C307, C309, C310, C311, C312, C504, C512: 2.2u; C_0402
C306, C308: 15p; C_0402
C501, C508: 2.2uf; C_0603
C505, C513: 10u; C_0603
C509: 100uf; CP_Tantalum_Case-B_EIA-3528-21_Reflow
C510: NP; C_0402
D301: TPD2EUSB30DRTR; SOT-3
D302: BLUE; LED_0603
D303: GREEN; LED_0603
D304: RED; LED_0603
F401: 0.5A polyfuse; R_1812
J101: USB_B_Micro; USB_Micro-B_Vertical_Molex-105133-0001
J102: Conn_02x14_Odd_Even; FLE-113-01-G-DV
J301: SWD; JST_SH_SM06B-SRSS-TB_06x1.00mm_Angled
J401, J402, J403: Conn_01x02; JST_PH_B2B-PH-K_02x2.00mm_Straight
K101: SERVO; JST_PH_B3B-PH-K_03x2.00mm_Straight
L501: 3.3uH; L_Bourns_SRN-4018
L502: xxuh; L_Bourns_SRN-4018
P101: CANBUS; JST_PH_B4B-PH-K_04x2.00mm_Straight
P102: Serial3; JST_SH_SM04B-SRSS-TB_04x1.00mm_Angled
P103: CTRL_SIGNALS; JST_PH_B7B-PH-K_07x2.00mm_Straight
P104: SPI; JST_SH_SM06B-SRSS-TB_06x1.00mm_Angled
P105: Serial1/tim4; JST_SH_SM04B-SRSS-TB_04x1.00mm_Angled
P106: I2C; JST_SH_SM04B-SRSS-TB_04x1.00mm_Angled
P107: HALL/Encoder; JST_PH_B6B-PH-K_06x2.00mm_Straight
Q401, Q402: IRLML6344TRPBF; SOT-23-3
R101: 100R; R_0402
R102, R103: 100k; R_0402
R104, R105: 22R; R_0402
R106, R107, R108: 2k2; R_0402
R109: 10k; R_0402
R201: 220R; R_0603
R301, R302, R303, R501: 1k; R_0402
R502: R33.2k 0.1%; R_0402
R503: 10k 0.1%; R_0402
U201: TJA1051TK-3; DFN-8-1EP_3x3mm_Pitch0.65mm
U301: STM32F40X_LQFP64; lqfp64_pad_mod
U501: AZ1117-5.0; SOT-223-3_TabPin2
U502: TPS561201; SOT-23-6
X301: 8MHz 10ppm; Oscillator_SMD_EuroQuartz_XO53-4pin_5.0x3.2mm

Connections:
+3V3: C202.1, C302.2, C305.2, C307.2, C309.2, C310.2, C311.2, C312.2, C507.1, C508.1, C509.1, C510.1, C511.1, J301.1, L501.1, L502.2, P102.3, P103.1, P104.1, P105.3, P106.3, P107.1, R106.2, R107.2, R108.2, R109.2, R301.2, R502.1, U201.5, U301.1, U301.13, U301.19, U301.32, U301.48, U301.64
+5V: C201.1, C504.1, C505.1, C512.1, C513.1, U201.3, U501.2
+12V: C501.1, C502.1, C503.1, F401.1, R501.2, U501.3, U502.3
/12vbuck_SENSE: C111.1, J102.8, U301.21
/12vgatedrive: J102.2, J102.4
/PHASE_CURRENT_1_ADC: C103.1, J102.11, U301.8
/PHASE_CURRENT_2_ADC: C104.1, J102.19, U301.9
/PHASE_CURRENT_3_ADC: C105.1, J102.26, U301.10
/PHASE_V_1_ADC: C107.1, J102.9, U301.14
/PHASE_V_2_ADC: C108.1, J102.17, U301.15
/PHASE_V_3_ADC: C109.1, J102.25, U301.16
/aux_outputs/AUX1_PWM: Q401.1, U301.22
/aux_outputs/AUX2_PWM: Q402.1, U301.23
/sheet5B3977DF/CANH: P101.3, R201.1, U201.7
/sheet5B3977DF/CANL: P101.2, R201.2, U201.6
/sheet5B3977DF/CAN_RX: U201.4, U301.61
/sheet5B3977DF/CAN_TX: U201.1, U301.62
/sheet5B3977E0/ADC_BRAKE: P103.4, R103.1, U301.27
/sheet5B3977E0/ADC_TEMP: C102.1, U301.24
/sheet5B3977E0/ADC_THROTTLE: P103.3, R102.1, U301.26
/sheet5B3977E0/ADC_VBUS: C106.1, U301.11
/sheet5B3977E0/HALL_1: P107.3, R106.1, U301.37
/sheet5B3977E0/HALL_2: P107.4, R107.1, U301.38
/sheet5B3977E0/HALL_3: P107.5, R108.1, U301.39
/sheet5B3977E0/LED_GREEN: R302.2, U301.3
/sheet5B3977E0/LED_RED: R303.2, U301.4
/sheet5B3977E0/SCL_2: P106.1, U301.29
/sheet5B3977E0/SDA_2: P106.2, U301.30
/sheet5B3977E0/SERVO: C101.2, R101.1, U301.17
/sheet5B3977E0/SPI3_MISO: P104.3, U301.56
/sheet5B3977E0/SPI3_MOSI: P104.2, U301.53
/sheet5B3977E0/SPI3_NSS: P104.5, U301.50
/sheet5B3977E0/SPI3_SCK: P104.4, U301.55
/sheet5B3977E0/TEMP_MOTOR: C110.2, P107.2, R109.1, U301.25
/sheet5B3977E0/USART1_RX: P105.1, U301.59
/sheet5B3977E0/USART1_TX: P105.2, U301.58
/sheet5B3977E0/USART3_RX: P102.1, U301.52
/sheet5B3977E0/USART3_TX: P102.2, U301.51
/sheet5B3977E0/USB_DM: D301.2, R105.1, U301.44
/sheet5B3977E0/USB_DP: D301.1, R104.1, U301.45
/sheet5B3977E0/VCAP1: C303.2, U301.31
/sheet5B3977E0/VCAP2: C301.2, U301.47
GND: C101.1, C102.2, C103.2, C104.2, C105.2, C106.2, C107.2, C108.2, C109.2, C110.1, C111.2, C201.2, C202.2, C301.1, C302.1, C303.1, C304.1, C305.1, C306.2, C307.1, C308.2, C309.1, C310.1, C311.1, C312.1, C501.2, C502.2, C503.2, C504.2, C505.2, C507.2, C508.2, C509.2, C511.2, C512.2, C513.2, D301.3, D302.2, D303.2, D304.2, J101.5, J101.6, J102.1, J102.3, J102.18, J102.20, J301.3, K101.3, P101.1, P102.4, P103.2, P103.7, P104.6, P105.4, P106.4, P107.6, R102.2, R103.2, R503.2, U201.2, U201.8, U201.9, U301.12, U301.18, U301.60, U301.63, U501.1, U502.1, X301.3
GNDPWR: J403.2, Q401.2, Q402.2
NRST: C304.2, J301.5, U301.7
unnamed: C306.1, U301.5, X301.1
unnamed: C308.1, U301.6, X301.2
unnamed: C506.1, L501.2, U502.2
unnamed: C506.2, U502.6
unnamed: C510.2, R502.2, R503.1, U502.4
unnamed: D302.1, R301.1
unnamed: D303.1, R302.1
unnamed: D304.1, R303.1
unnamed: F401.2, J401.1, J402.1, J403.1
unnamed: J101.2, R105.2
unnamed: J101.3, R104.2
unnamed: J401.2, Q401.3
unnamed: J402.2, Q402.3
unnamed: K101.1, R101.2
unnamed: R501.1, U502.5
SWCLK: J301.2, U301.49
SWDIO: J301.4, U301.46

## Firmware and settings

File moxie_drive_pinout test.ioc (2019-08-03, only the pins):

Mcu.UserName=STM32F405RGTx
PA0-WKUP.Signal=ADCx_IN0
PA1.Signal=ADCx_IN1
PA10.Signal=S_TIM1_CH3
PA11.Signal=USB_OTG_FS_DM
PA12.Signal=USB_OTG_FS_DP
PA13.Signal=SYS_JTMS-SWDIO
PA14.Signal=SYS_JTCK-SWCLK
PA2.Signal=ADCx_IN2
PA3.Signal=S_TIM5_CH4
PA4.Signal=COMP_DAC1_group
PA5.Signal=COMP_DAC2_group
PA6.Signal=S_TIM13_CH1
PA7.Signal=S_TIM14_CH1
PA8.Signal=S_TIM1_CH1
PA9.Signal=S_TIM1_CH2
PB0.Signal=ADCx_IN8
PB1.Signal=ADCx_IN9
PB10.Signal=I2C2_SCL
PB11.Signal=I2C2_SDA
PB13.Signal=TIM1_CH1N
PB14.Signal=TIM1_CH2N
PB15.Signal=TIM1_CH3N
PB3.Signal=SPI3_SCK
PB4.Signal=SPI3_MISO
PB6.Signal=USART1_TX
PB7.Signal=USART1_RX
PB8.Signal=CAN1_RX
PB9.Signal=CAN1_TX
PC0.Signal=ADCx_IN10
PC1.Signal=ADCx_IN11
PC10.Signal=USART3_TX
PC11.Signal=USART3_RX
PC12.Signal=SPI3_MOSI
PC2.Signal=ADCx_IN12
PC3.Signal=ADCx_IN13
PC4.Signal=ADCx_IN14
PC5.Signal=ADCx_IN15
PC6.Signal=GPIO_Input
PC7.Signal=GPIO_Input
PC8.Signal=GPIO_Input
PC9.Signal=RCC_MCO_2
